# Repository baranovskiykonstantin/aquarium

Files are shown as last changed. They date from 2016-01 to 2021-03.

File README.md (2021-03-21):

# DIY Aquarium Controller

## Features
* The controller is based on ATMEL's microcontroller ATMEGA8A
    * Settings are stored in EEPROM
    * Detecting a system hang with Watchdog.
* Remote control via Bluetooth
    * HC-05 module
    * RFCOMM protocol
    * Baud rate 9600 bps
* LED lighting
    * 12V DC output
    * 400mA max.
    * Adjustable brightness
    * Adjustable gradual turning on/off (0-30 min)
    * Adjustable time of turning on/off the light
* Thermostat
    * 220V AC output
    * 3A max. (fused)
    * Adjustable the min. and max. temperature thresholds
* Water temperature measurement
    * DS18B20 sensor
    * Accuracy 0.5 °C
    * Error detecting
* On-board RTC
    * DS1302 chip
    * Adjustable date&time
    * Adjustable daily time correction
    * Backup battery
* 4-digits LED display
    * Two modes of displaying: the current time or the temperature of the water
* Touch control
    * Touch Sensor 1 to switch displaying mode (time -> temperature -> time -> ...)
    * Touch Sensor 1 and Sensor 2 at the same time to switch the operation mode (on -> off -> auto -> on -> ...) of:
        * the lighting if the display shows the time;
        * the heater if the display shows the temperature;
* [Aquarium-control app](https://github.com/baranovskiykonstantin/aquarium-control) is designed to setup the aquarium settings (Windows, Linux, Android, [Symbian](https://github.com/baranovskiykonstantin/AquariumControlS60))

## Wiring diagram
wiring-diagram

1. Capacitive sensors (aluminum scotch 10x50mm on inner side of the top cover)
2. Mains plug
3. Aquarium controller PCB
4. Power supply PCB
5. Bluetooth module HC-05
6. LEDs (4 x 1W = 12V 300mA)
7. Waterproof DS18B20
8. Heater

## HC-05 configuration
* Change the indicating mode
   * By default LED is blinking on idle and lighting on connecting
   * Disconnect output LED2(31) from PCB's pad that is going to the LED and connect this pad to LED1(32) output
   * Now LED is not lighting on idle and lighting on connecting
* Restore default settings
   * Enter to AT-command mode
   * Send command `AT+ORGL`
* Set device name
   * Enter to AT-command mode
   * Send command `AT+NAME=aquarium` (the device's name must begin with "aquarium" to be recognized by aquarium-control app)
* Reduce power consumption (from ~40mA to ~3mA on idle!)
   * Enter to AT-command mode
   * Send command `AT+IPSCAN=1024,1,1024,1`

## Communicating with the controller
After establishing a connection, you can send commands to the aquarium
controller to setup it.<br>
If a command has the correct format and can be successfully completed the
controller will send OK response. If the command has the wrong format, the
controller will send ERROR response. If the controller receives an unknown
command it will send UNKNOWN response.<br>
The command must end with `\n` or `\r`. If the value of a parameter is bigger
than allowed one it will be reduced to max. allowed value.

### Command `status`
Get information about current state of the aquarium.

Format:

`status`

Response:

```
Date: 01.01.17 Friday
Time: 13:29:59 (-3 sec at 12:00:00)
Temp: 22
Heat: OFF auto (20-22)
Light: ON manual (10:00:00-20:00:00) 43/50% 10min
Display: time
```

Meaning:

Line 1: the current date and the day of the week;<br>
Line 2: the current time and the information about the daily time correction;<br>
Line 3: the temperature of the water (°C);<br>
Line 4: the thermostat status:<br>
* `ON` - the heater is on, `OFF` - the heater is off
* `auto` - automatic mode, `manual` - manual mode
* the value in the parentheses indicates the temperature range that maintains in the automatic mode<br>

Line 5: the lighting status:<br>
* `ON` - the light is on, `OFF` - the light is off
* `auto` - automatic mode, `manual` - manual mode
* the value in the parentheses indicates the period of time when the light is on in the automatic mode<br>
* at the end, the current/target brightness level in percent and the light rising time in minutes

Line 6: the display mode (`time` - the current time is shown, `temp` - the temperature of the water is shown)

### Command `date`
Set a date.

Format:

`date DD.MN.YY W`

Parameters:<br>
* `DD` - day of the month (01-31)
* `MN` - month (01-12)
* `YY` - year (00-99)
* `W` - day of the week (1 - Monday ... 7 - Sunday)

Response:

`OK` or `ERROR`

### Command `time`
Set a time and/or a time correction

Format 1:

`time HH:MM:SS`

Parameters:<br>
* `HH` - hours (00-23)
* `MM` - minutes (00-59)
* `SS` - seconds (00-59)

Format 2:

`time +CC`<br>
`time -CC`

Parameters:<br>
* `+` or `-` - add or subtract the time correction value
* `CC` - time correction in seconds (00-59)

Format 3:

`time HH:MM:SS +CC`<br>
`time HH:MM:SS -CC`

Parameters:<br>
* `HH` - hours (00-23)
* `MM` - minutes (00-59)
* `SS` - seconds (00-59)
* `+` or `-` - add or subtract the time correction value
* `CC` - time correction in seconds (00-59)

Response:

`OK` or `ERROR`

### Command `heat`
Heater setup.

Format 1:

`heat LO-HI`

Parameters:<br>
* `LO` - minimal temperature (18-35)
* `HI` - maximal temperature (18-35)

Format 2:

`heat on`<br>
`heat off`<br>
`heat auto`<br>

Parameters:<br>
* `on` - switch to the manual mode and turn on heater
* `off` - switch to the manual mode and turn off heater
* `auto` - switch to the automatic mode

Response:

`OK` or `ERROR`

### Command `light`
Lighting setup.

Format 1:

`light H1:M1:S1-H2:M2:S2`

Parameters:<br>
* `H1:M1:S1` - light on time (00:00:00-23:59:59)
* `H2:M2:S2` - light off time (00:00:00-23:59:59)

Format 2:

`light on`<br>
`light off`<br>
`light auto`<br>

Parameters:<br>
* `on` - switch to the manual mode and turn on light
* `off` - switch to the manual mode and turn off light
* `auto` - switch to the automatic mode

Format 3:

`light level LLL`

Parameters:<br>
* `LLL` - brightness level in percent (000-100)

Format: 4:

`light rise RR`

Parameters:<br>
* `RR` - time of the light rising in minutes (00-30)

Format: 5:

`light H1:M1:S1-H2:M2:S2 LLL RR`

Parameters:<br>
* `H1:M1:S1` - time of turn on light (00:00:00-23:59:59)
* `H2:M2:S2` - time of turn off light (00:00:00-23:59:59)
* `LLL` - brightness level (000-100)
* `RR` - light rising time (00-30)

Response:

`OK` or `ERROR`

### Command `display`
Display setup.

Format:

`display time`<br>
`display temp`

Parameters:<br>
* `time` - show the current time
* `temp` - show the current temperature of the water

Response:

`OK` or `ERROR`

### Command `reboot`
Restart the program.

Format:

`reboot`

Response:

`OK`

### Command `help`
Print the list of available commands.

Format:

`help`

Response:

```
Available commands:

status
date DD.MN.YY W
time HH:MM:SS
time +CC
time -CC
time HH:MM:SS +CC
time HH:MM:SS -CC
heat LO-HI
heat on
heat off
heat auto
light H1:M1:S1-H2:M2:S2
light level LLL
light rise RR
light H1:M1:S1-H2:M2:S2 LLL RR
light on
light off
light auto
display time
display temp
reboot
help

```

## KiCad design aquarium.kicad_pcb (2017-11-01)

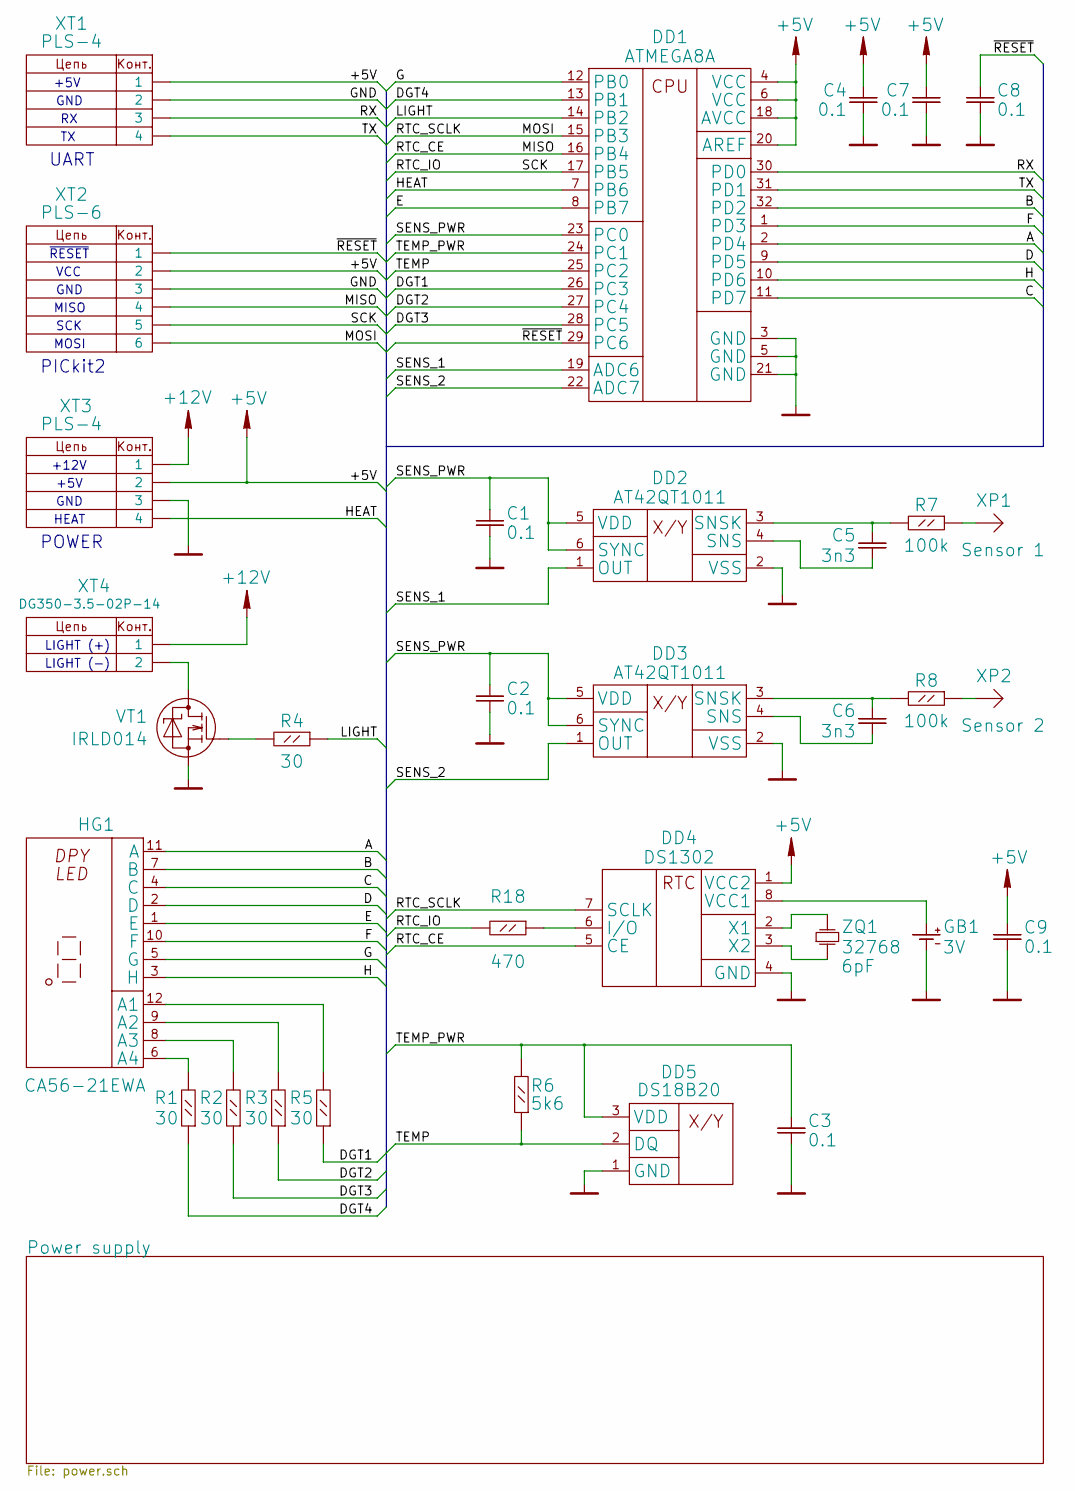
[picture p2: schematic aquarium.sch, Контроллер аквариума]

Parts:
C1, C2, C3, C4, C7, C8, C9: 0.1; SMD_0805
C5, C6: 3n3; SMD_0805
DD1: ATMEGA8A; TQFP32-30
DD2, DD3: AT42QT1011; SOT23-6
DD4: DS1302; DIP8-300
DD5: DS18B20; PLS-3
GB1: 3V; CR2032_H
HG1: CA56-21EWA; 56-21_smd
R1, R2, R3, R4, R5: 30; R_0805
R6: 5k6; R_0805
R7, R8: 100k; R_0805
R18: 470; R_0805
VT1: IRLD014; HVMDIP
XP1: Sensor 1; PLS-1
XP2: Sensor 2; PLS-1
XT1, XT3: PLS-4
XT2: PLS-6
XT4: DG350-3.5-02P-14; DG-350-2
ZQ1: 32768; HC_3.0x8.0mm

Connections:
+5V: C4.1, C7.1, C9.1, DD1.4 (VCC), DD1.6 (VCC), DD1.18 (AVCC), DD1.20 (AREF), DD4.1 (VCC2), XT1.1, XT2.2, XT3.2; also elsewhere on the board
+12V: XT3.1, XT4.1; also elsewhere on the board
/A: DD1.2 (PD4), HG1.11 (A)
/B: DD1.32 (PD2), HG1.7 (B)
/C: DD1.11 (PD7), HG1.4 (C)
/D: DD1.9 (PD5), HG1.2 (D)
/DGT1: DD1.26 (PC3), R5.1
/DGT2: DD1.27 (PC4), R3.1
/DGT3: DD1.28 (PC5), R2.1
/DGT4: DD1.13 (PB1), R1.1
/E: DD1.8 (PB7), HG1.1 (E)
/F: DD1.1 (PD3), HG1.10 (F)
/G: DD1.12 (PB0), HG1.5 (G)
/H: DD1.10 (PD6), HG1.3 (H)
/HEAT: DD1.7 (PB6), XT3.4
/LIGHT: DD1.14 (PB2), R4.1
/MISO: DD1.16 (PB4), DD4.5 (CE), XT2.4
/MOSI: DD1.15 (PB3), DD4.7 (SCLK), XT2.6
/RTC_IO: DD1.17 (PB5), R18.2, XT2.5
/RX: DD1.30 (PD0), XT1.3
/SENS_1: DD1.19 (ADC6), DD2.1 (OUT)
/SENS_2: DD1.22 (ADC7), DD3.1 (OUT)
/SENS_PWR: C1.1, C2.1, DD1.23 (PC0), DD2.5 (VDD), DD2.6 (SYNC), DD3.5 (VDD), DD3.6 (SYNC)
/TEMP: DD1.25 (PC2), DD5.2 (DQ), R6.1
/TEMP_PWR: C3.1, DD1.24 (PC1), DD5.3 (VDD), R6.2
/TX: DD1.31 (PD1), XT1.4
/~RESET: C8.1, DD1.29 (PC6), XT2.1
GND: C1.2, C2.2, C3.2, C4.2, C7.2, C8.2, C9.2, DD1.3 (GND), DD1.5 (GND), DD1.21 (GND), DD2.2 (VSS), DD3.2 (VSS), DD4.4 (GND), DD5.1 (GND), GB1.2 (-), VT1.3 (S), XT1.2, XT2.3, XT3.3; also elsewhere on the board
unnamed: C5.1, DD2.3 (SNSK), R7.2
unnamed: C5.2, DD2.4 (SNS)
unnamed: C6.1, DD3.3 (SNSK), R8.2
unnamed: C6.2, DD3.4 (SNS)
unnamed: DD4.2 (X1), ZQ1.2
unnamed: DD4.3 (X2), ZQ1.1
unnamed: DD4.6 (I/O), R18.1
unnamed: DD4.8 (VCC1), GB1.1 (+)
unnamed: HG1.6 (A4), R1.2
unnamed: HG1.8 (A3), R2.2
unnamed: HG1.9 (A2), R3.2
unnamed: HG1.12 (A1), R5.2
unnamed: R4.2, VT1.2 (G)
unnamed: R7.1, XP1.1
unnamed: R8.1, XP2.1
unnamed: VT1.1 (D), XT4.2

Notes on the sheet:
LIGHT (+)
LIGHT (-)
+5V
GND
UART
PICkit2
MISO
VCC
SCK
MOSI
~RESET
HEAT
+12V
POWER

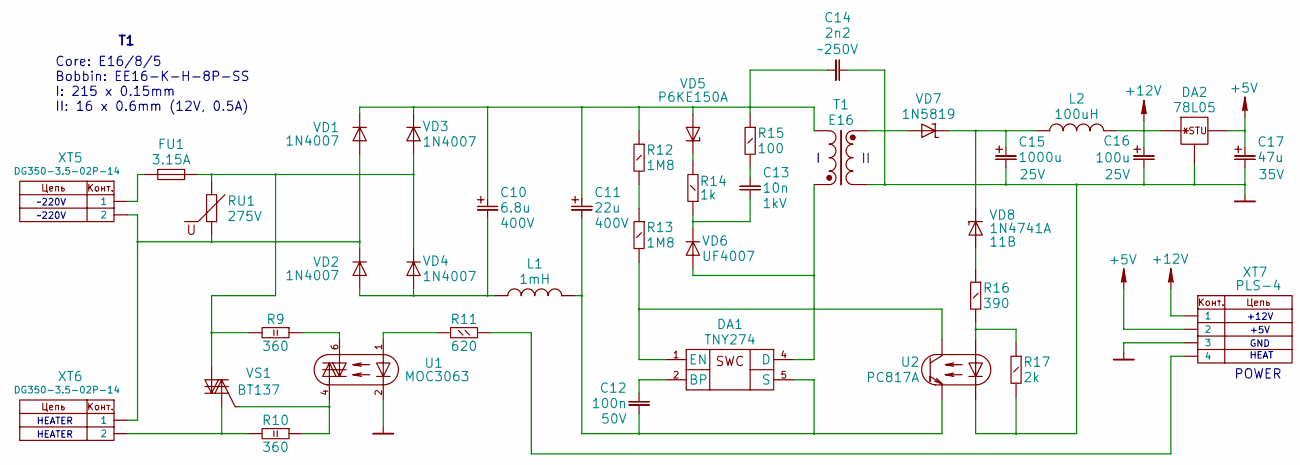
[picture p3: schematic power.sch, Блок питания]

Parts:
C10: 6.8u; CPH_5_10x16mm
C11: 22u; CPH_5_13x25mm
C12: 100n; C_5x3mm
C13: 10n; C_5x3mm
C14: 2n2; C_7.5x4mm
C15: 1000u; CPH_5_10x20mm
C16: 100u; CP_2.5x6mm
C17: 47u; CP_2.5x5mm
DA1: TNY274; PDIP-8C
DA2: 78L05; TO92-250
FU1: 3.15A; FU_5x20mm
L1: 1mH; Ind_5x8mm
L2: 100uH; Ind_5x8mm
R9, R10: 360; RH_2
R11: 620; RH_0.25
R12, R13: 1M8; RV_0.25
R14: 1k; RV_0.25
R15: 100; RV_0.25
R16: 390; RV_0.25
R17: 2k; RV_0.25
RU1: 275V; FNR-05
T1: E16; E16_5_10mm
U1: MOC3063; DIP6-300
U2: PC817A; DIP4-300
VD1, VD2, VD3, VD4: 1N4007; DO-41
VD5: P6KE150A; DO-15
VD6: UF4007; DO-41
VD7: 1N5819; DO-41
VD8: 1N4741A; DO-41
VS1: BT137; TO220
XT5, XT6: DG350-3.5-02P-14; DG-350-2
XT7: PLS-4

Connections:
+5V: C17.1, DA2.1 (OUT), XT7.2; also elsewhere on the board
+12V: C16.1, DA2.3 (IN), L2.2, XT7.1; also elsewhere on the board
GND: C14.1, C15.2, C16.2, C17.2, DA2.2 (GND), R17.2, T1.4 (S2), U1.2 (K), U2.2 (K), XT7.3; also elsewhere on the board
unnamed: C10.1, C11.1, C14.2, R12.1, R15.1, T1.2, VD1.2 (K), VD3.2 (K), VD5.1 (A)
unnamed: C10.2, L1.1, VD2.1 (A), VD4.1 (A)
unnamed: C11.2, C12.2, DA1.5 (S), L1.2, U2.3 (E)
unnamed: C12.1, DA1.2 (BP)
unnamed: C13.1, R15.2
unnamed: C13.2, R14.1, VD6.2 (K)
unnamed: C15.1, L2.1, VD7.2 (K), VD8.2 (K)
unnamed: DA1.1 (EN), R13.2, U2.4 (C)
unnamed: DA1.4 (D), T1.1, VD6.1 (A)
unnamed: FU1.1, XT5.1
unnamed: FU1.2, R9.2, RU1.2, VD3.1 (A), VD4.2 (K), VS1.2
unnamed: R9.1, U1.6 (MT)
unnamed: R10.1, U1.4 (MT), VS1.3 (G)
unnamed: R10.2, VS1.1, XT6.2
unnamed: R11.1, U1.1 (A)
unnamed: R11.2, XT7.4
unnamed: R12.2, R13.1
unnamed: R14.2, VD5.2 (K)
unnamed: R16.1, VD8.1 (A)
unnamed: R16.2, R17.1, U2.1 (A)
unnamed: RU1.1, VD1.1 (A), VD2.2 (K), XT5.2, XT6.1
unnamed: T1.3 (S1), VD7.1 (A)

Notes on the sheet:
~~220V
HEATER
+5V
HEAT
+12V
GND
POWER
Core: E16/8/5 Bobbin: EE16-K-H-8P-SS I: 215 x 0.15mm II: 16 x 0.6mm (12V, 0.5A)

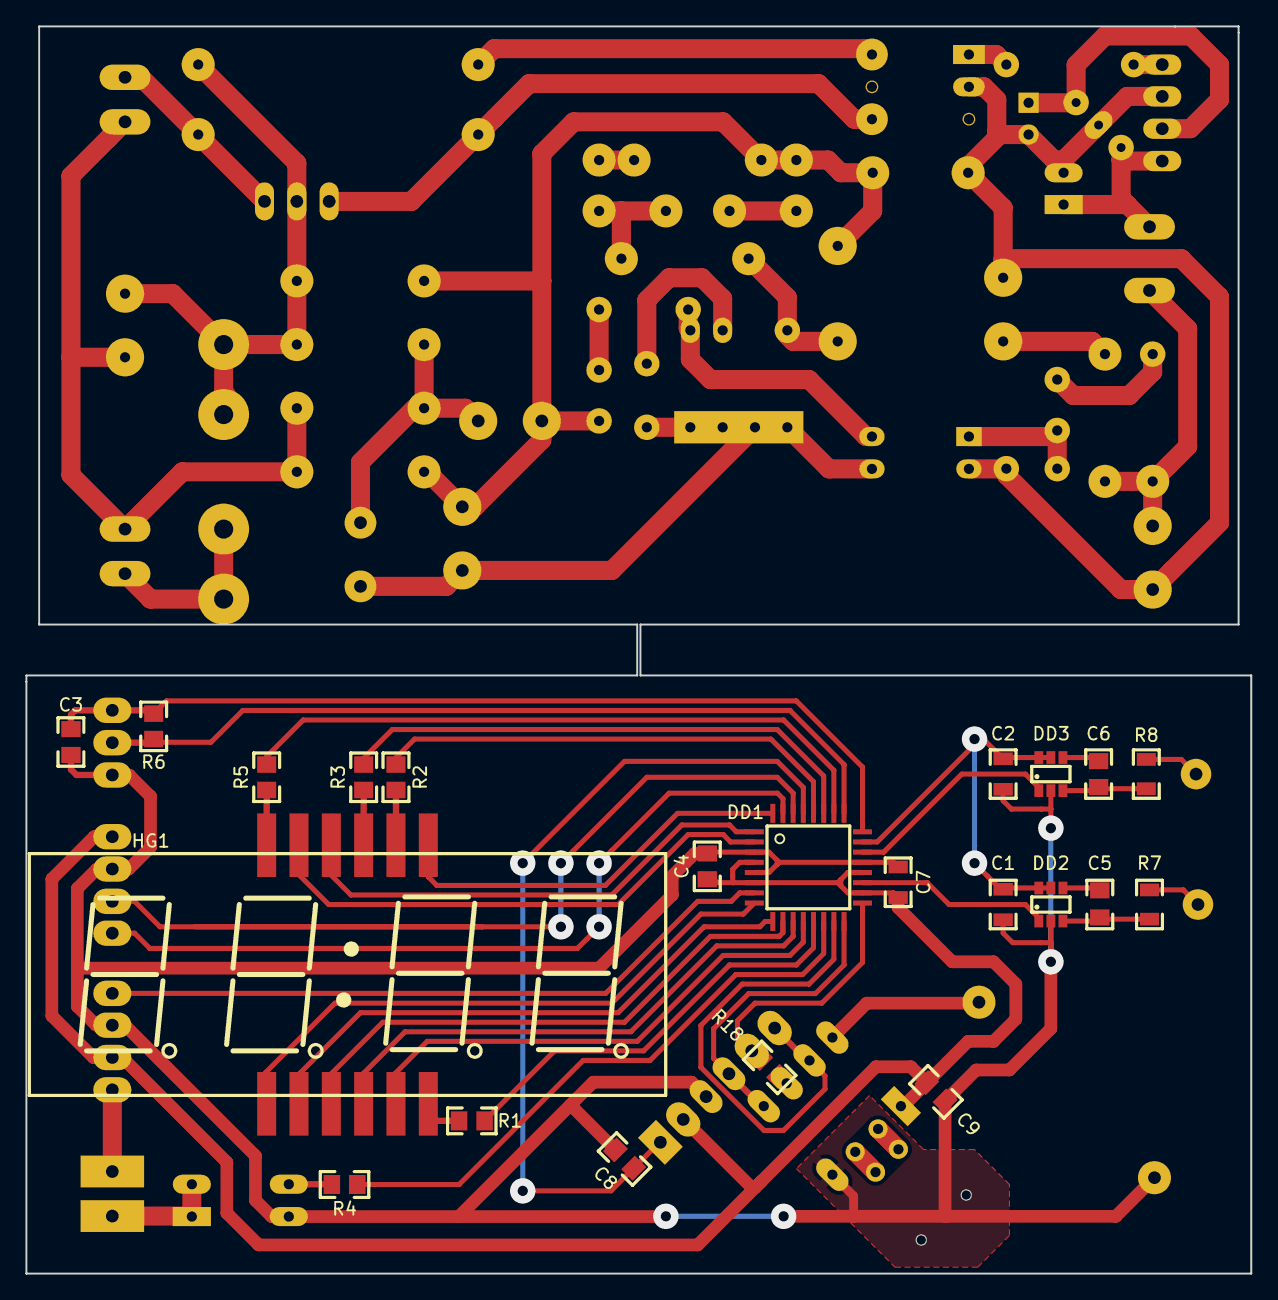
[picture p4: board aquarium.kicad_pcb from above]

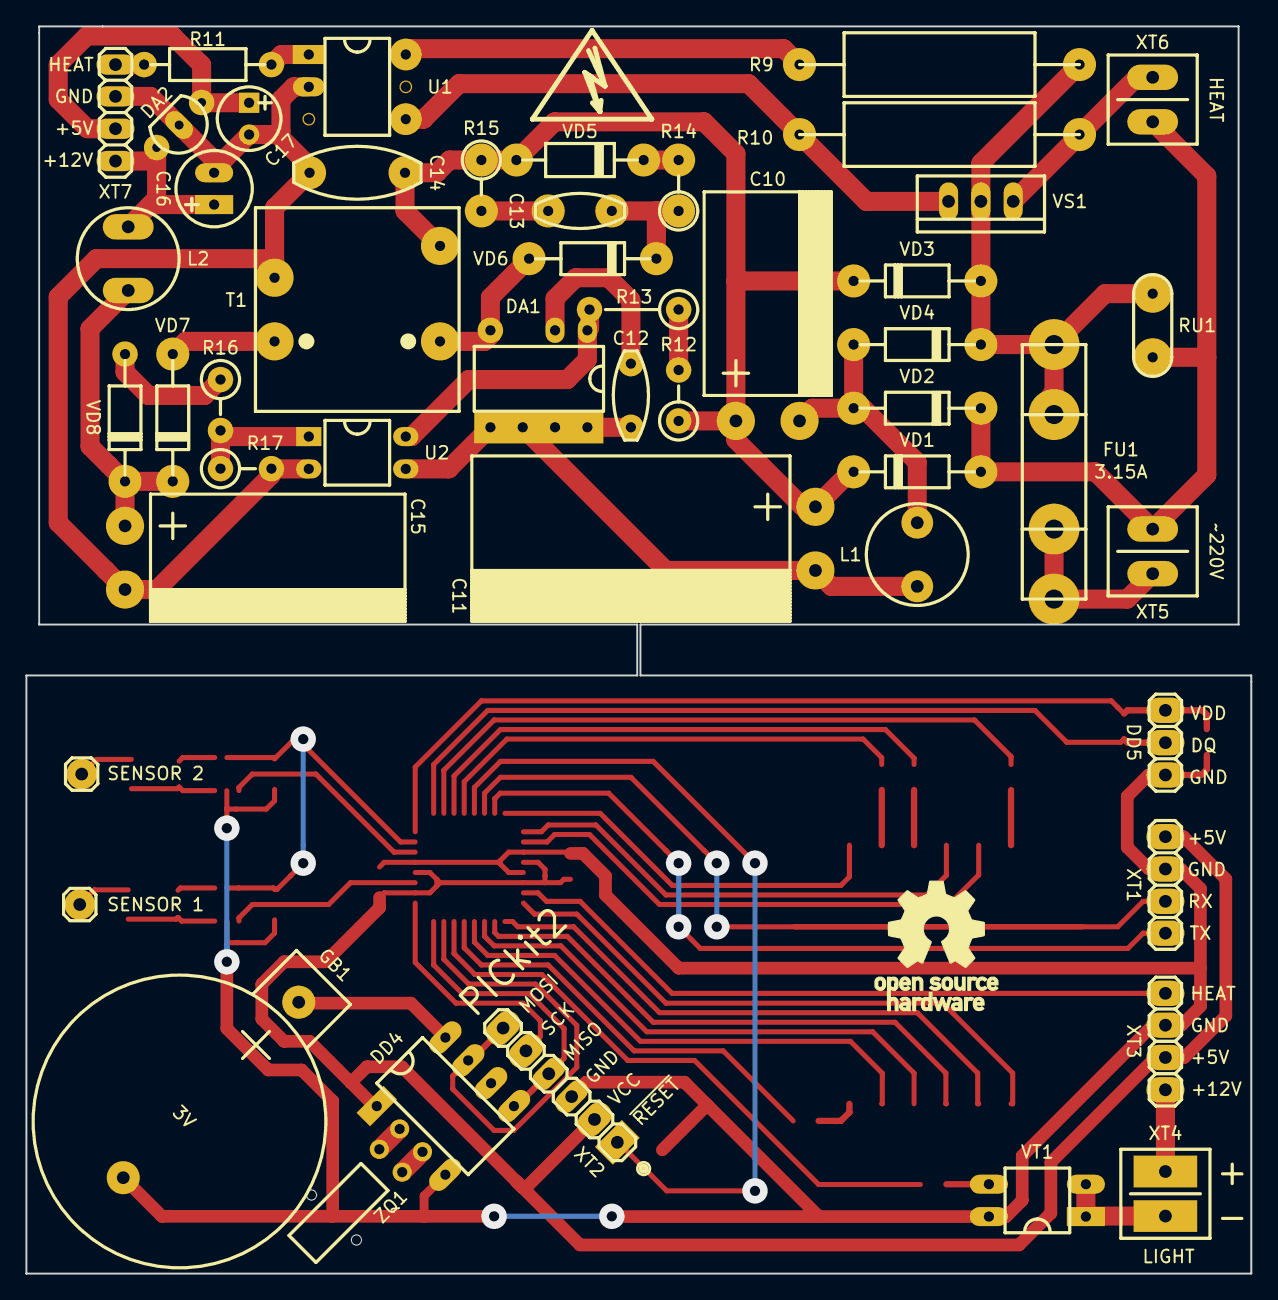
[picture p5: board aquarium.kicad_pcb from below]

Board: 2 copper layers, 96.2 x 98.0 mm, 71 parts (49 on the bottom side), 66 nets.

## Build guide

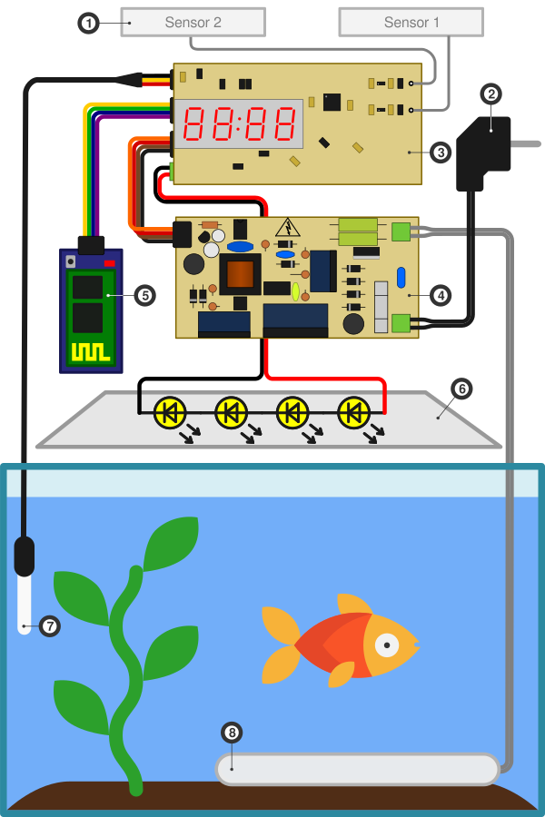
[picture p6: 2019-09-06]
images/wiring-diagram.png

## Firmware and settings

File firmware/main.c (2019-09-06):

/* Name: main.c
 * Project: aquarium
 * Author: Baranovskiy Konstantin
 * Creation Date: 2015-12-28
 * Tabsize: 4
 * Copyright: (c) 2017-2019 Baranovskiy Konstantin
 * License: GNU GPL v3 (see License.txt)
 */

#include <avr/io.h>
#include <avr/wdt.h>

#include "aquarium.h"

int main(void)
{
    uint16_t loop_counter = 0;

    wdt_enable(WDTO_1S);

    aquarium_init();

    while (1)
    {
        wdt_reset();

        if (++loop_counter > 5000)
        {
            loop_counter = 0;
        }

        if ((loop_counter % 1000) == 0)
        {
            aquarium_process_time();

            if (loop_counter == 2000)
            {
                aquarium_process_sensors();
            }

            if (loop_counter == 3000)
            {
                aquarium_process_heat();
            }

            if (loop_counter == 5000)
            {
                aquarium_process_light();
            }
        }

        aquarium_process_uart();
    }
}

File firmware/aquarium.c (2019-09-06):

/* Name: aquarium.c
 * Project: aquarium
 * Author: Baranovskiy Konstantin
 * Creation Date: 2019-08-25
 * Tabsize: 4
 * Copyright: (c) 2019 Baranovskiy Konstantin
 * License: GNU GPL v3 (see License.txt)
 */

#include <util/delay.h>
#include <avr/interrupt.h>
#include <avr/eeprom.h>
#include <avr/pgmspace.h>
#include <stdlib.h>
#include <string.h>

#include "aquarium.h"
#include "datetime.h"
#include "display.h"
#include "adc.h"
#include "pwm.h"
#include "ds18b20.h"
#include "ds1302.h"
#include "uart.h"

/*
 * I/O configuration
 */
#define HEAT_AS_OUT DDRB |= (1 << PB6)
#define HEAT_ON PORTB |= (1 << PB6)
#define HEAT_OFF PORTB &= ~(1 << PB6)
#define HEAT_STATE (PINB & (1 << PB6)) >> PB6

#define SENSORS_PWR_AS_OUT DDRC |= (1 << PC0)
#define SENSORS_PWR_ON PORTC |= (1 << PC0)
#define SENSORS_PWR_OFF PORTC &= ~(1 << PC0)
#define SENSORS_PWR_STATE (PINC & (1 << PC0)) >> PC0

/*
 * Displaying modes
 */
#define SHOW_TIME 1
#define SHOW_TEMP 2

/*
 * Operating modes
 */
#define MODE_AUTO 'a'
#define MODE_MANUAL 'm'

/*
 * UART responses
 */
#define OK 2
#define ERROR 4
#define UNKNOWN 8

static struct
{
    // Displaying mode
    uint8_t display;

    // Temperature of the water
    int8_t temperature;

    struct
    {
        // Current date and time
        datetime_t now;
        // Date and time of last time adjustment
        datetime_t adjusted;
        // Time correction value
        time_t correction;
    } clock;

    struct
    {
        // Lighting mode
        uint8_t mode;
        // Time of turning light on
        time_t time_on;
        // Time of turning light off
        time_t time_off;
        // Brightness of light in percent
        uint8_t level;
        // Time of light rising from 0 to 100 % in minutes
        uint8_t risetime;
    } light;

    struct
    {
        // Heating mode
        uint8_t mode;
        // Temperature of turning heater on
        int8_t temp_l;
        // Temperature of turning heater off
        int8_t temp_h;
    } heater;

    struct
    {
        // Characters received from UART
        uint8_t buffer[UART_RX_BUFFER_SIZE];
        // Position in buffer for storing next received char from UART
        uint8_t index;
    } uart;

} aquarium;

static struct {
    uint8_t temp_l;
    uint8_t temp_h;

    uint8_t time_on_hour;
    uint8_t time_on_min;
    uint8_t time_on_sec;

    uint8_t time_off_hour;
    uint8_t time_off_min;
    uint8_t time_off_sec;

    uint8_t daily_corr_sign;
    uint8_t daily_corr_sec;

    uint8_t heat_mode;
    uint8_t light_mode;
    uint8_t display_mode;

    uint8_t light_level;
    uint8_t light_rise_time;

} config EEMEM = {
// "config" stores some important values of "aquarium" structure in EEPROM.
// Default values:
    22, 25,
    8, 0, 0,
    18, 0, 0,
    '+', 0,
    MODE_AUTO,
    MODE_AUTO,
    SHOW_TIME,
    50, 15
};

static const char help_msg[] PROGMEM = "\r\nAvailable commands:\r\n\r\n"
                                       "status\r\n"
                                       "date DD.MN.YY W\r\n"
                                       "time HH:MM:SS\r\n"
                                       "time +CC\r\n"
                                       "time -CC\r\n"
                                       "time HH:MM:SS +CC\r\n"
                                       "time HH:MM:SS -CC\r\n"
                                       "heat LO-HI\r\n"
                                       "heat on\r\n"
                                       "heat off\r\n"
                                       "heat auto\r\n"
                                       "light H1:M1:S1-H2:M2:S2\r\n"
                                       "light level LLL\r\n"
                                       "light rise RR\r\n"
                                       "light H1:M1:S1-H2:M2:S2 LLL RR\r\n"
                                       "light on\r\n"
                                       "light off\r\n"
                                       "light auto\r\n"
                                       "display time\r\n"
                                       "display temp\r\n"
                                       "reboot\r\n"
                                       "help\r\n\r\n";

/* ------------------------------------------------------------------------- *
 * Send response about command processing to UART
 * ------------------------------------------------------------------------- */
static void uart_response(uint8_t response)
{
    switch (response)
    {
        case OK:
            uart_puts("OK\r\n");
            break;
        case ERROR:
            uart_puts("ERROR\r\n");
            break;
        default:
            uart_puts("UNKNOWN\r\n");
    }
}

/* ------------------------------------------------------------------------- *
 * Send int to UART as ASCII
 * ------------------------------------------------------------------------- */
static void uart_puti(int8_t value, uint8_t padding_zeros)
{
    if (value < 0 )
    {
        uart_putc('-');
    }

    if (labs(value) >= 100 || padding_zeros >= 3)
    {
        uart_putc(labs(value) / 100 + 0x30);
    }

    if (labs(value) >= 10 || padding_zeros >= 2)
    {
        uart_putc(labs(value) % 100 / 10 + 0x30);
    }

    uart_putc(value % 10 + 0x30);
}

/* ------------------------------------------------------------------------- *
 * Check if char is digit
 * ------------------------------------------------------------------------- */
static uint8_t chr_is_digit(uint8_t chr)
{
    if (chr >= '0' && chr <= '9')
    {
        return 1;
    }
    return 0;
}

/* ------------------------------------------------------------------------- *
 * Extract integer from buffer
 * ------------------------------------------------------------------------- */
static uint8_t extract_int(uint8_t offset, uint8_t len)
{
    uint8_t value = 0;
    uint8_t i;

    for (i = 0; i < len; i++)
    {
        value *= 10;
        value += (aquarium.uart.buffer[offset + i] - 0x30);
    }

    return value;
}

/* ------------------------------------------------------------------------- *
 * Extract time from UART buffer
 * ------------------------------------------------------------------------- */
static void extract_time(uint8_t offset)
{
    uint8_t value;

    value = extract_int(offset, 2);
    aquarium.clock.now.hour = value > 23 ? 23 : value;

    value = extract_int((offset + 3), 2);
    aquarium.clock.now.min =value > 59 ? 59 : value;

    value = extract_int((offset + 6), 2);
    aquarium.clock.now.sec = value > 59 ? 59 : value;

    aquarium.clock.now.H12_24 = H24;
    aquarium.clock.now.AMPM = AM;

    aquarium.clock.adjusted = aquarium.clock.now;

    ds1302_write_datetime(&(aquarium.clock.now));
    ds1302_write_datetime_to_ram(&(aquarium.clock.adjusted), 0);
}
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

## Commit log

2016-01-18 Initial commit.
    [aquarium.kicad_pcb, aquarium.sch]
2016-01-18 ATmega48PA changet to ATmega8A
    [aquarium.kicad_pcb, aquarium.sch]
2016-01-18 Added noise filtering to sensor input.
    [main.c]
2016-01-27 Added possibility to calibrate the capacitive sensor.
    [aquarium.kicad_pcb, aquarium.sch]
2016-02-04 Revert "Added possibility to calibrate the capacitive sensor."
    This reverts commit 56735a840efcf7c901892eb1b50b215983c0ef84.
    [aquarium.kicad_pcb, aquarium.sch]
2016-02-08 Corrected sensitivity of the sensor and added noise protection on Reset pin.
    [aquarium.kicad_pcb, aquarium.sch]
2016-02-18 Small correction of the comments.
    [main.c]
2016-02-21 Added daily time correction and more UART commands.
    [ds1302.h, main.c]
2016-02-22 Changed capacity of the reference capacitor of the sensor IC. Corrected initialization of the time correction variable.
    [aquarium.sch]
2016-03-24 Preventing EEPROM corruption on power off.
2016-03-24 Updated README.md and schematic image.
2016-05-15 Add photo of the aquarium.
    [aquarium.kicad_pcb]
2016-12-05 * Renamed command ''state'' to ''status''. * Enabled watchdog timer. * Optimized work with DS18B20.
2017-01-05 Added new file of worksheet frame.
2017-01-16 New version of the controller (schematic and pcb).
    [aquarium.kicad_pcb, aquarium.sch, power.sch]
2017-01-30 Small changes to PCB.
    [aquarium.kicad_pcb, power.sch]
2017-02-05 Finished working on PCB.
    [aquarium.kicad_pcb, aquarium.sch]
2017-03-11 Udated firmware for new version of the schematic.
2017-03-11 New version of the schematic and PCB's.
    [aquarium.kicad_pcb, aquarium.sch, power.sch]
2017-03-12 Remove optional capacitor from schematic.
    [aquarium.sch]
2017-04-16 Firmware updates: * fixed time correction; * changed main loop processing; * added sensor signal filtering.
    [display.c, main.c]
2017-11-01 README totally reworked.
    [aquarium.kicad_pcb, aquarium.sch, power.sch]
2017-11-03 Fix temp sersor errors counting.
    [main.c]
2019-09-22 Note about BT-device naming was added.
2019-09-24 Schematic/PCB update to the latest KiCad.
    [aquarium.sch, power.sch]
